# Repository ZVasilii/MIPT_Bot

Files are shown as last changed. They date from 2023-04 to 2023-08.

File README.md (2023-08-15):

# "Двухколесный робот"



## Введение

Данный проект был реализован на курсе от "Физтех.Фабрики" в 2023 году. Курс создан чтобы познакомить студентов 4 курса с основами прототипирования и проектирования, а так же обучить их прикладным технологиям.  (3D печать, лазерная резка и т.д.)

### Авторы

Студенты 4 курса ФРКТ:

Зайцев Василий  
Быков Алексей  
Касков Михаил  

## Задача

Преодолеть полосу препятствий за наименьшее время на роботе с нестандартными колесами


## Конструкция робота

В основе движения нашего робота мы решили использовать идею переноса веса относительно оси вращения больших внешних колёс, подобно хомяку в колесе. 
Повороты были реализованы за счёт танкого управления.

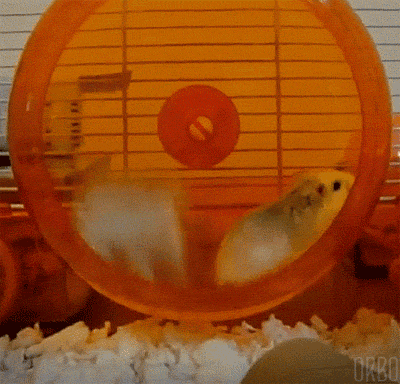
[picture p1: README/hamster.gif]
gif


### Этапы конструирования

1) В первую очередь надо было проверить работоспособность идеи. Поэтому была создана простейшая конструкция, даже не имеющая беспроводного управления.



---

2) После того, как стало понятно, что всё работает, мы решили что в нашем движении необходимо больше плавности и момента, нежели скорости. Поэтому необходимо было сделать редуктор: выбор пал на планетарную передачу в силу малых размеров, эстетики и интересных расчётов. Так же добавили беспроводное управление. Пульт управления состоял из одного джойстика, с которого бралось 2 оси как в танковом управлении.




---

3) Всё было прекрасно до первого падения с 20см горки, поэтому мы укрепили корпус поперечинами между ограничителями колёс. Так же была выявлена проблема с прохождением ванной с маршмеллоу, так как колёса узкие и вся конструкция  закапывалась вниз и садилась на корпус. Для решения данной проблемы сделали поперечные штыри на колёса.



---

4) Управляющая сторона была собрана на макетной плате. Затем был разработан пульт дистанционного управления. Дополнительно были подключены кнопка и тумблер для дополнительных действий, в частности - включения освещения.



---

5) Для прохождения тонеля мы добавли ленту WS2812, и запрограммировали её в виде полицейской мигалки.

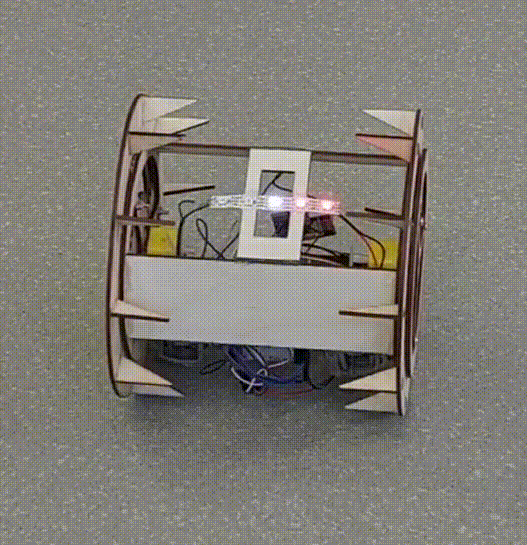
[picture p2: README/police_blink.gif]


---

### Используемые компоненты

**Робот**

* Arduino Mega 2560 (можно и Arduino Uno)
* Motor Shield
* NRF24L01 с платой питания
* Светодиодная лента на 5 ячеек WS2812
* Фанера 4мм
* Болты и гайки М4

**Пульт управления**

* Arduino Uno (можно использовать любую)
* NRF24L01 с платой питания
* Кнопка
* Тумблер
* 2 джойстика
* *на время запуска нужно питание платы, подойдёт питание от USB повербанком или любым другим способом*

---

### Механическая часть

В папке `src` лежит файл `robot_parts.dxf` с `dxf` исходниками для вырезания деталей робота на лазере.



---

### Схема подключения компонентов

Робот

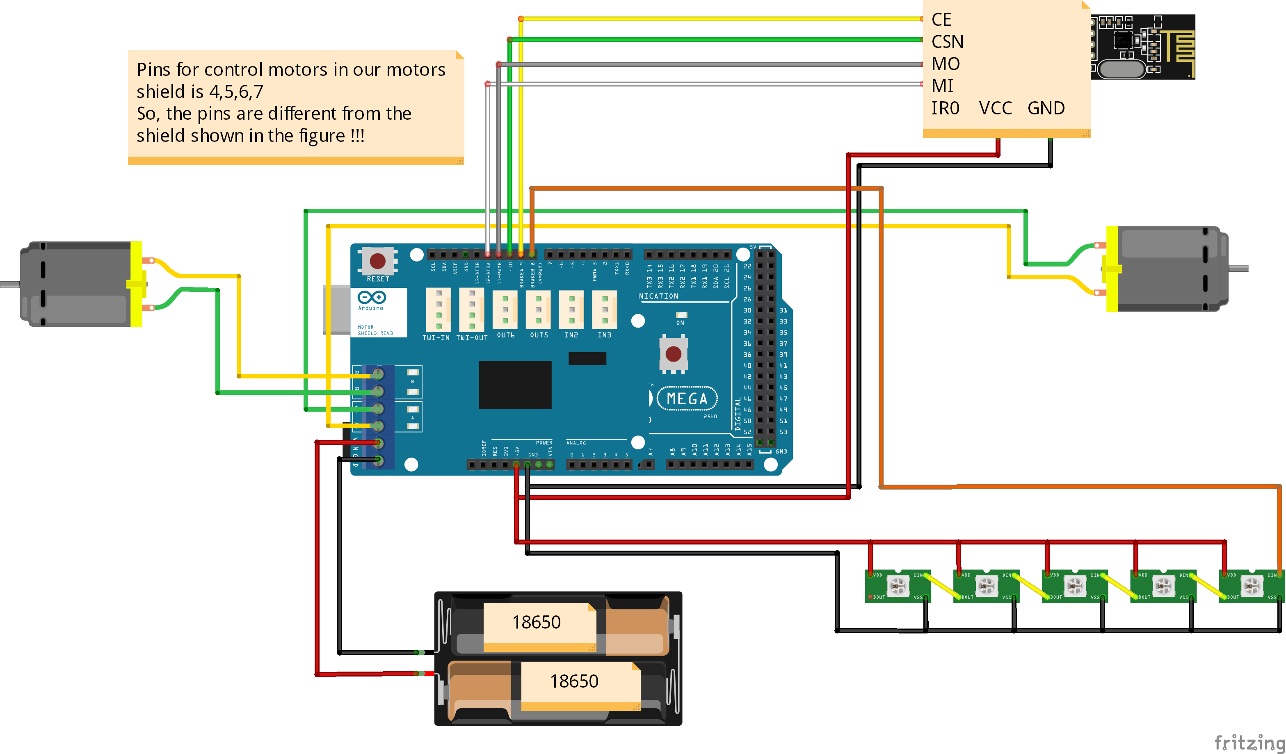
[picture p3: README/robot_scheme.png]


---

Пульт управления

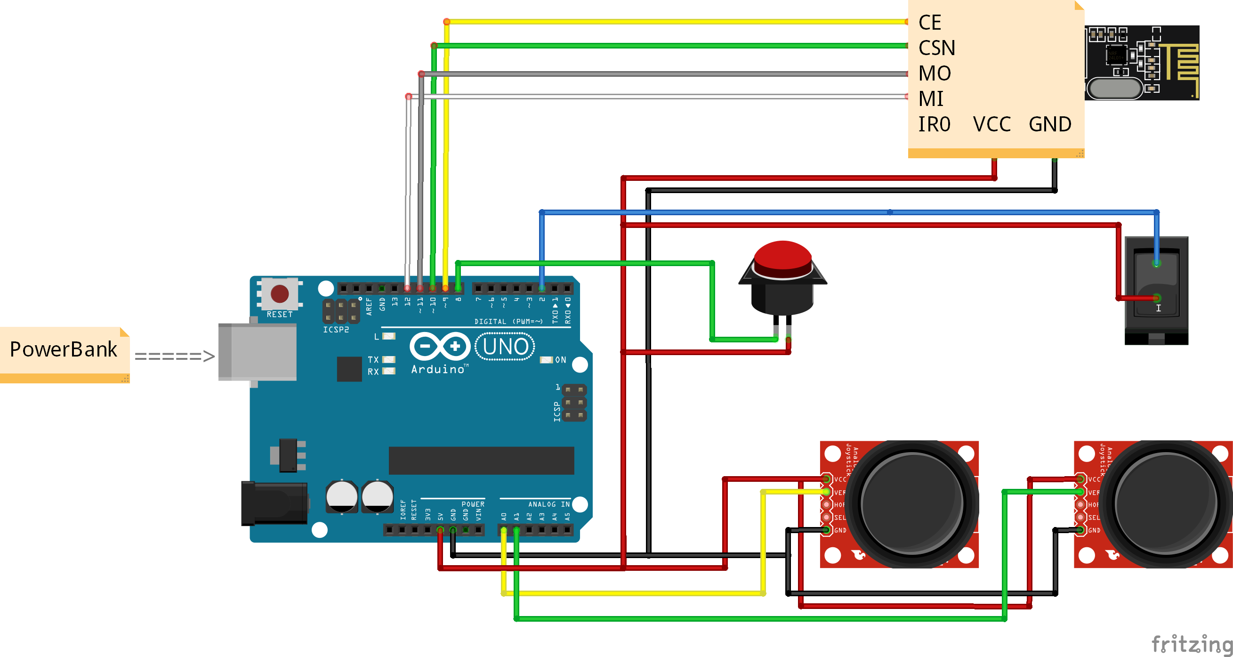
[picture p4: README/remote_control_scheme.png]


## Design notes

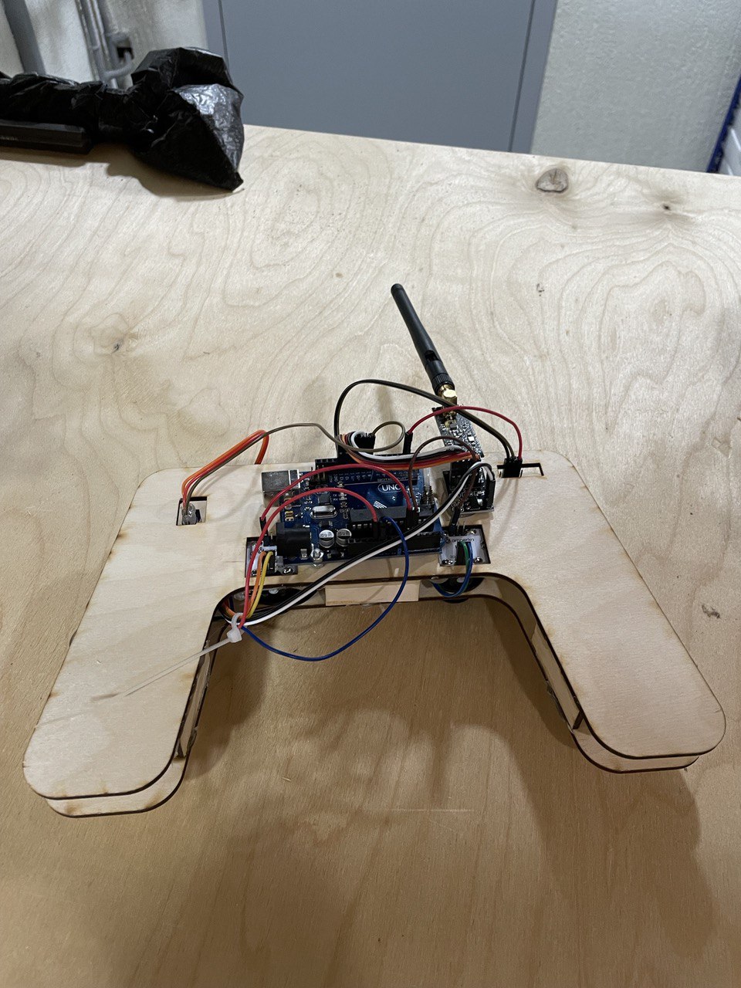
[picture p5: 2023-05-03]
README/remote_controller_bottom.jpg

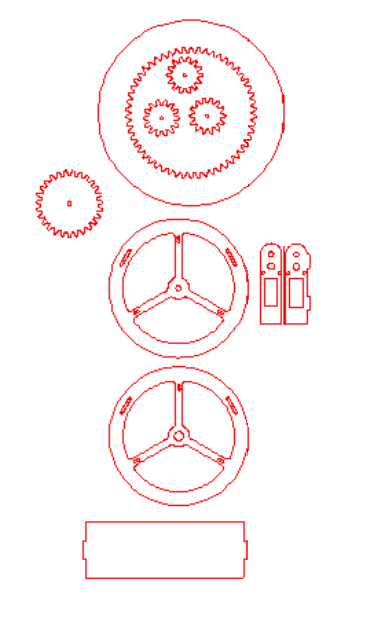
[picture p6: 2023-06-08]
README/dxf_preview.png

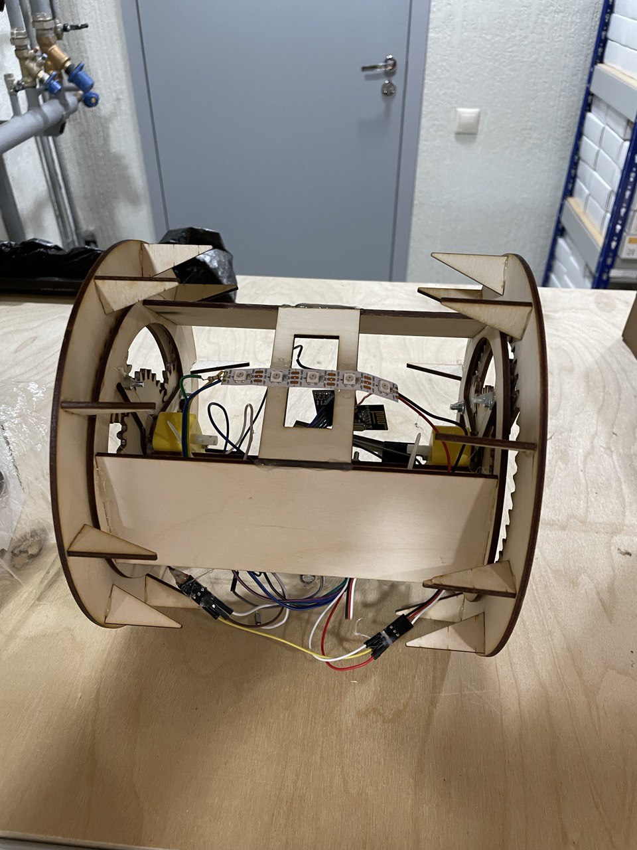
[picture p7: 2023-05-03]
README/robot.jpg

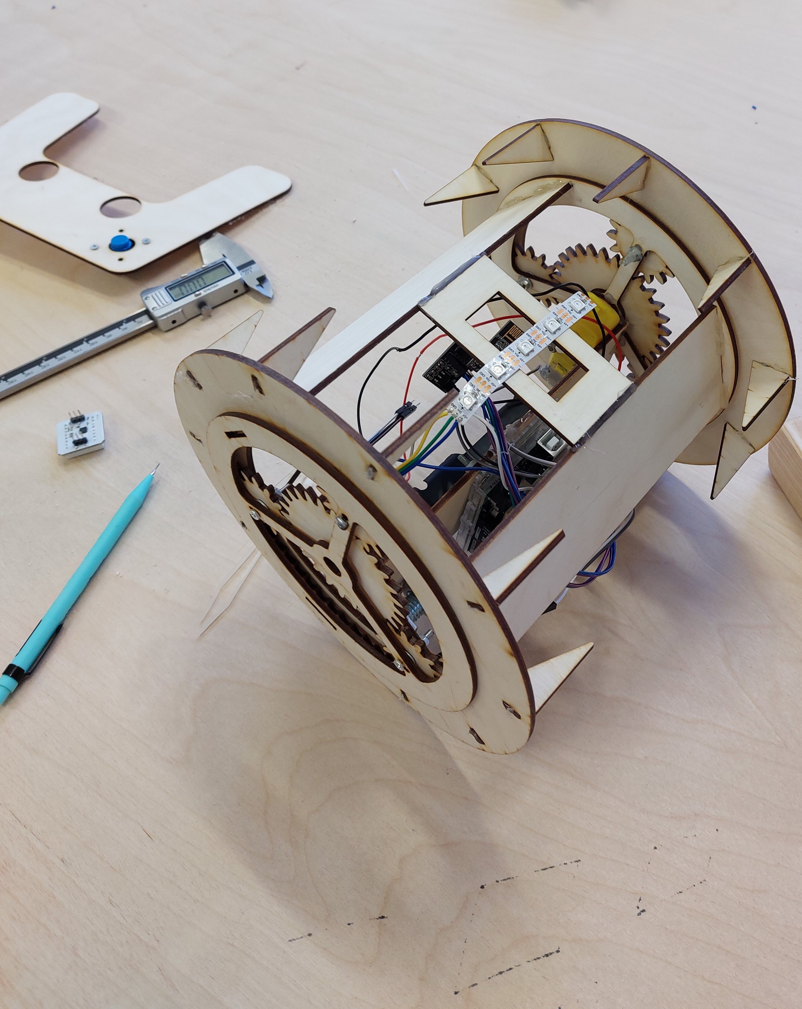
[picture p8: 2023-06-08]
README/robot_1-4.jpg

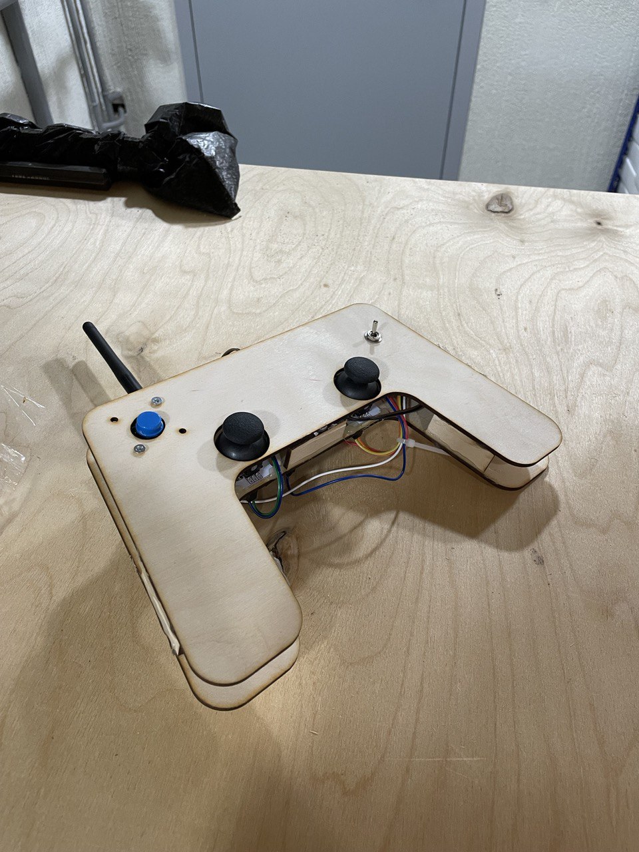
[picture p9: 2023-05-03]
README/remote_controller_top.jpg

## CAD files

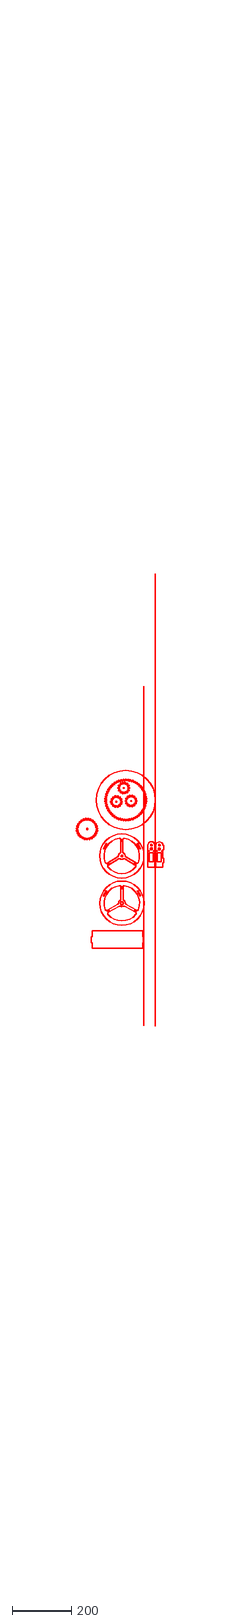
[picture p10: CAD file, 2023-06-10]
src/robot_parts.dxf
295.4 x 5301.9

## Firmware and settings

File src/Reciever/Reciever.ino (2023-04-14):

#include <SPI.h>
#include <nRF24L01.h>
#include <RF24.h>
#include <Servo.h>

#include "Common.h"
#include "MotorControl.h"
#include "FastLED.h"

const char RFPin0 = 9;
const char RFPin1 = 10;

const int PIN_LED = 8;
const int SERVO_PIN = 2;
const int NUM_LEDS = 5;
const int LED_HOLD = 500;
const int LED_HOLD_double = 200;

int LED_state = 0;
int LED_ON;
int SERVO_ON;
CRGB leds[NUM_LEDS];
Servo srv;


void set_led_state_0()
{
  leds[0] = CRGB::Black;
  leds[1] = CRGB::Black;
  leds[2] = CRGB::White;
  leds[3] = CRGB::Red;
  leds[4] = CRGB::Red;
  LED_state = 0;
  FastLED.show();
}

void set_led_state_1()
{
  leds[0] = CRGB::Blue;
  leds[1] = CRGB::Blue;
  leds[2] = CRGB::White;
  leds[3] = CRGB::Black;
  leds[4] = CRGB::Black;
  LED_state = 1;
  FastLED.show();
}

void set_led_state_2()
{
  for (int i = 0; i < NUM_LEDS; i++)
    leds[i] = CRGB::Black;
  LED_state = 2;
  FastLED.show();
}

void toggle_led()
{
  if (LED_ON)
  {
    if (LED_state)
    {
      set_led_state_0();
    }
    else
      set_led_state_1();
  }
  else
  {
   set_led_state_2();
  }
    
}

RF24 rmRcv(RFPin0, RFPin1);


void setup() {
  initMotorControl();
  rmRcv.begin();
  rmRcv.setChannel(1);
  rmRcv.setDataRate(RF24_1MBPS);
  rmRcv.setPALevel(RF24_PA_HIGH);
  rmRcv.openReadingPipe(0, 0x1234567877LL);
  rmRcv.startListening();
  FastLED.addLeds<WS2812, PIN_LED, GRB>(leds, NUM_LEDS);
  FastLED.setBrightness(255);
  srv.attach(SERVO_PIN);

  Serial.begin(9600);
}

void loop() {

  static unsigned long lastTimestampSwitch = millis();
  
  if (millis() - lastTimestampSwitch > LED_HOLD)
  {
    toggle_led();
    lastTimestampSwitch = millis();
  }
  
  Command cmd;
  if (rmRcv.available())
  {
    rmRcv.read(&cmd, sizeof(cmd));
    //Serial.println(String(cmd.speedLeft) + " " + String(cmd.speedRight));
    LED_ON = cmd.LED_ON;
    SERVO_ON = cmd.SERVO_ON;
    setPowerOnMotors(cmd.speedLeft, cmd.speedRight);
    Serial.println(String(cmd.SERVO_ON));
    if (SERVO_ON)
      srv.write(80);
     else
      srv.write(180);

    // Serial.println(String(tmp[1]));
  }

}

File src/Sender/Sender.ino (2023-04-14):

#include <SPI.h>
#include <nRF24L01.h>
#include <RF24.h>

#include "Common.h"

const char RFPin0 = 9;
const char RFPin1 = 10;
const char LED_PIN = 8;
const char SERVO_PIN = 2;
const char JOY_LEFT_PIN = A0;
const char JOY_RIGHT_PIN = A1;

RF24 rmSnd(RFPin0, RFPin1);


void setup() {
  rmSnd.begin();
  rmSnd.setChannel(1);
  rmSnd.setDataRate(RF24_1MBPS);
  rmSnd.setPALevel(RF24_PA_HIGH);
  rmSnd.openWritingPipe(0x1234567877LL);
  rmSnd.stopListening();
  pinMode(LED_PIN, INPUT_PULLUP);
  pinMode(SERVO_PIN, INPUT);

  //Serial.begin(9600);

}

void loop() {
  uc left = analogRead(JOY_LEFT_PIN) / 4;
  uc right = analogRead(JOY_RIGHT_PIN) / 4;
  int LED_ON = digitalRead(LED_PIN);
  int SERVO_ON = digitalRead(SERVO_PIN);
  
  
  Command cmd(left, right, LED_ON, SERVO_ON);
  rmSnd.write(&cmd, sizeof(cmd));
  //Serial.println(String(left) + " " + String(right) + String(SERVO_ON));

}

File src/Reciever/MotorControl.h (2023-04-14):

const int M_LEFT_PIN = 6;
const int M_RIGHT_PIN = 5;
const int ROT_RIGHT_PIN = 4;
const int ROT_LEFT_PIN = 7;
const int JOY_PIN = A0;


enum MOTOR {LEFT, RIGHT};
enum ROTATION {FORWARD, BACKWARD};

void setRotation(int rotationPin, ROTATION rotation);
void setSpeedRotation(MOTOR motor, ROTATION rotation, int speed);

void initMotorControl() {
  pinMode(M_LEFT_PIN, OUTPUT);
  pinMode(M_RIGHT_PIN, OUTPUT);
  pinMode(ROT_RIGHT_PIN, OUTPUT);
  pinMode(ROT_LEFT_PIN, OUTPUT);
}

int16_t rattlingOff(int16_t value)
{
  if (abs(value) < 5) 
    return 0;
  return value;  
}

int16_t rattlingOffCenter(int16_t value)
{
  int16_t error = 8;
  int16_t middle = 256 / 2;
  if (abs(value - middle) < error) 
    return 0;
  return map(abs(value - middle), error, middle, 1, 255);  
}

void setPowerOnMotors(int16_t leftMotor, int16_t rightMotor)
{
  int16_t middle = 256 / 2;

  setSpeedRotation(LEFT, (leftMotor - middle) > 0 ? FORWARD : BACKWARD , rattlingOffCenter(leftMotor));
  setSpeedRotation(RIGHT, (rightMotor - middle) > 0 ? FORWARD : BACKWARD, rattlingOffCenter(rightMotor));
}

void setRotation(int rotationPin, ROTATION rotation)
{
  if (rotation)
    digitalWrite(rotationPin, HIGH);
  else
    digitalWrite(rotationPin, LOW);
}

void setSpeedRotation(MOTOR motor, ROTATION rotation, int speed)
{
  int rotationPin = -1;
  int motorPin = -1;

  if (motor == LEFT)
  {
    rotationPin = ROT_LEFT_PIN;
    motorPin = M_LEFT_PIN;
  }
  else
  {
    rotationPin = ROT_RIGHT_PIN;
    motorPin = M_RIGHT_PIN;
  }
  setRotation(rotationPin, rotation);
  analogWrite(motorPin, speed);
}

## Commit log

2023-03-24 Add motor controlling for PoC
2023-04-01 Added "tank" control of motors on robot
2023-05-03 add files for cutting the robot parts
    [robot_parts.dxf]
2023-06-08 Prepare data for readme
    [remote_control.fzz, robot.fzz]
2023-06-10 changed path to CAD file
    [robot_parts.dxf]
